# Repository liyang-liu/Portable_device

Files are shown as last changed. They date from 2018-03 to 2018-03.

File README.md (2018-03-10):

# Portable_device

This is the website containing details for the "Portable Lifting Device" project as a joint project with studendents enrolled for Mechanical and Mechatronic 3 at University of Technology, Sydney.

The project has been successfully attempted by the 2017-Spring team (Mobitronic) and 2017-Autumn team (UP Engineering). 
In particular, Mobitronic has envestigated on the subject thoroughly and explored both pneumatic concept and  mechanical concept. A prototype pneumatic demo was made with an [inflatable matress](https://drive.google.com/file/d/0B8edSPbUCKdPTHlibjlWQjhMN2M). For meachnical design, a [scissor jack stool drawing](https//github.com/liyang-liu/Portable_device/src/2017_Autumn_Mobitronic/scissor_jack_concept.mp4) is developed with detailed force/pressure calculation.
The UP Engineeirng team has manufactured a [portable airbag](https://youtu.be/5JIshlNcmgY).

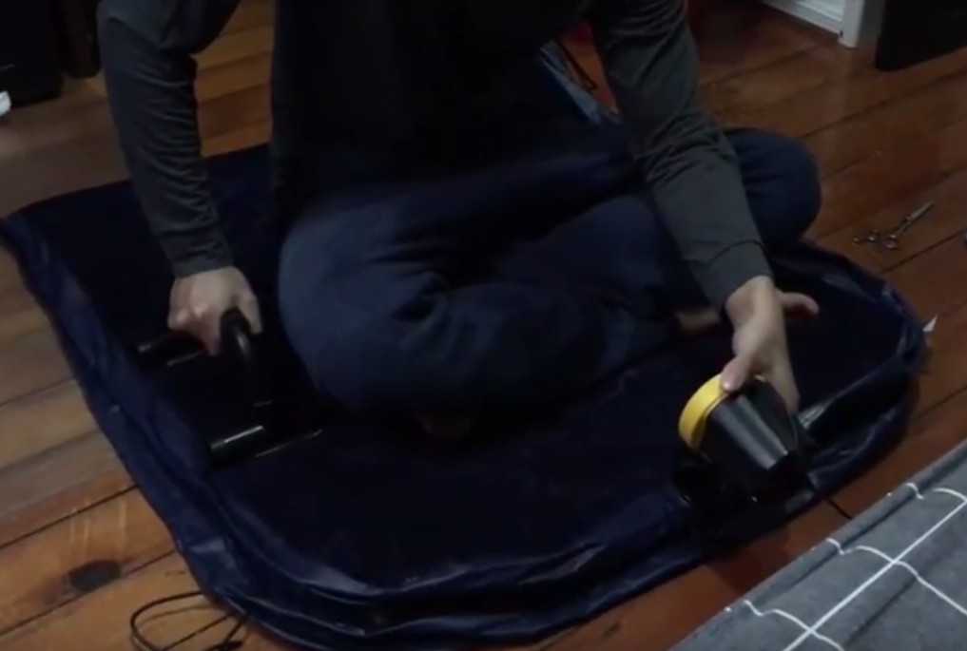
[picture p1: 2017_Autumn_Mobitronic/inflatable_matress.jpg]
inflatable_matress

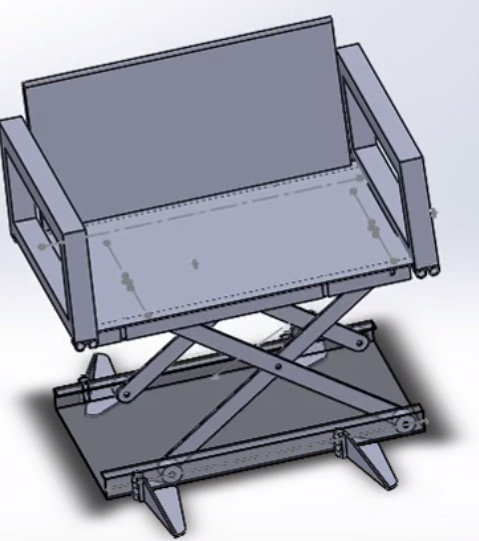
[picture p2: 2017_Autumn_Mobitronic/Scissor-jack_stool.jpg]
scissor-jack

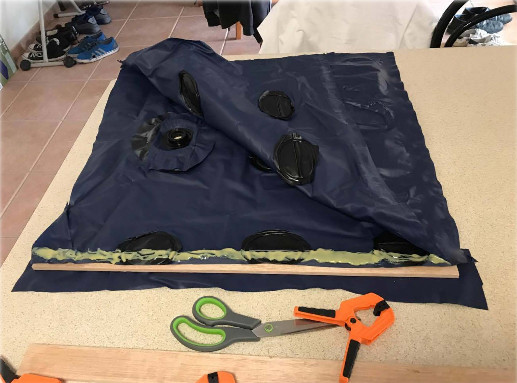
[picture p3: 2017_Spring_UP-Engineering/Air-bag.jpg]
portable_airbag


# 1. Prerequisites
Solidworks

# 2. Specification
Detailed specification is given in word document "Project_for_Lifting_airbag_spring-semester.docx"

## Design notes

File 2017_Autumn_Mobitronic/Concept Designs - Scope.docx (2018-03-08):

# Concept Designs – Scope

Team Mobitronic (13): Project: Portable Lifting Device

Renay Jewo (11443468) – Mechanical Engineer Client: Liyang Liu

Kunxian Huang (11671512) – Mechanical Engineer Project Start Date: 20/03/17

Bikrom Saha (11775677) – Mechanical Engineer Project Completion Date: 19/06/17

Viet Hung Doan (11808211) – Mechatronic Engineer

# Airbag Solution Concept Design

- Air-Bag Lifting mechanism will be connected to the client’s wheelchair from the back using connecting rods. The lifting device will contain a circular airbag that will be meshed between two platforms as shown below.
- The Air-Bag lifting capacity is more than sufficient to carry the patient. The Air-Bag will be inflated whilst the patient is seated using an Electric Pump that will be actuated by the patient using a toggle switch to pump and another to deflate.
- Transfer from surface to surface will be facilitated by the inclusion of hand-rails on either side of the top platform as depicted.
- Example air bag:

http://12.188.149.117/categories/lifting_air_bags/lowmedliftbags.aspx

Advantages | Disadvantages
Robust to hold weight of patient | Weight (Heavy) – Due to Electric Pump and Air Bag (Weight:Lifting Capacity Ratio)
Transported using wheelchair (Has wheels) | Not Hand-Portable – Will weigh more than 13kg
Electrically Operated (Electric Pump and Switches) – Easy to use and operate | Requires minor modification to wheelchair (Latch to connect lifting device)
Gradual raising of patient (not jolty)

# Alternative Hydraulic/Mechanical Concept Design (Hydraulic Jack)

- Hydraulic Jack used between two platforms to raise and lower the client to the specified heights of a wheelchair (500mm) and a kayak (350mm).
- Hydraulic Jack will be manually operated to raise and lower the platform by the patient. This doesn’t necessarily require much effort.
- The lifting device can in this case be smaller in dimensions, this will reduce the weight due to negating the electric pump and batteries from the design above.
- The topology of the design will be the similar to the air-bag lifting device in that it will be dragged behind the wheelchair and attached using a latch.

Advantages | Disadvantages
Lightweight Design | Hand-Operated (Manual Operation)
No external accessories such as a pump or heavy materials | Requires minor modification to wheelchair (Latch to connect lifting device)
Cheap and easy to operate, Height easily controlled
Transported using wheelchair

Airbag Proof of Concept – Testing

- We will be purchasing an inflatable mattress/airbag to simulate the effects and dynamics of raising and lowering the patient from deflation (once the patient is seated) to inflation.
- We will find a suitable pump to use within this experiment to provide enough pressure to lift the patient based on the specifications provided and to the required heights.
- This is just an experiment to determine the pressure required lift the patient.

Concept Designs – Specifications/Needs

The following specifications and functional requirements below are based on approximate values and are here to provide an indication and to accentuate the above advantages and disadvantages of each concept design.

| Airbag Concept Design | Hydraulic Concept Design
Weight (kg) | Gross Weight: ~15kg AirBag: 7kg Electric Pump: 3.9kg Batteries: 2kg Extras: 3kg | Total Weight: >5kg
Costs ($) | $2,500 | $300
Size (mm) | 800 x 600 x 250 | 600 x 600 x 200
Ease-of-use | Moderate | Easy

Questions to be clarified with stakeholder

1. Why is the lifting device needed?
2. What are the uses cases:
  1) Helps user to transfer to kayak
  2) 2nd scenario? To help user transfer to wheelchair in event of fall
3. Need to get a storyboard of user’s daily activity, to help understand motivation, use case and how the design can best suit user needs
4. How portable should the device be? Pump, power may take a lot of weight
  1) Will the device be carried independently by user for set up with other assistance?
5. Is a platform needed for the airbag to reside on top?

Portable Lifting DeviceTeam Mobitronic (13) 02/04/17

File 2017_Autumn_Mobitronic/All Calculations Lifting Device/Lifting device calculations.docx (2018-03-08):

# Lifting device calculations

The dimensions in this report base on the CAD model updated on 29 May 2017.

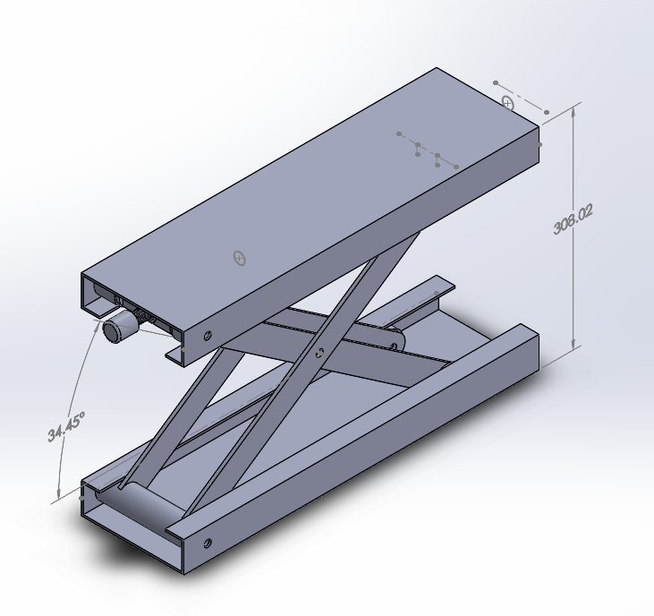
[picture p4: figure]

# Assumptions

Choosing lead screw SFU 3210-3 for initial calculations:

- Pitch diameter: 16mm
- Lead: 10mm
- Dynamic loading: 729kg
- Static loading: 1350kgf

Friction coefficient between steel screw and steel balls with machine oil: 0.15

User weight (W): 1000N (~101kg)

# Calculate Linear Force Acting on Lead Nut

Rx2

ti

ti

W

Rx2=w/(tan⁡(ti)) (see appendix for step by step)

The requirement height varies from 150mm to 500mm corresponding to ti from 13.28 to 78.66 degree.

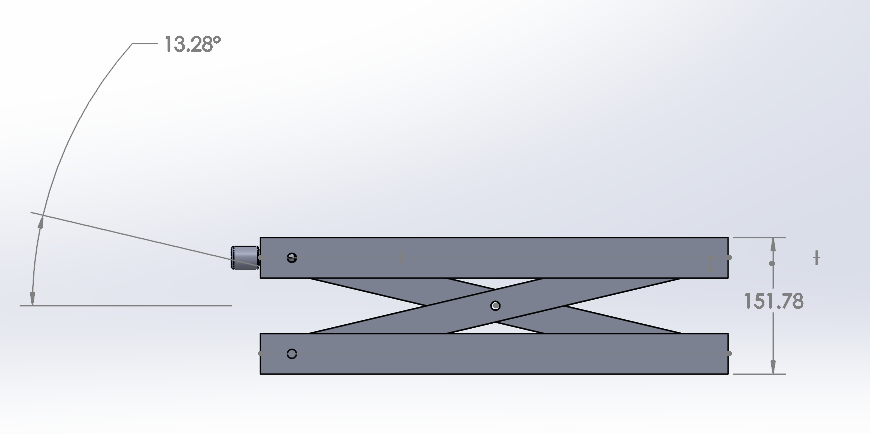
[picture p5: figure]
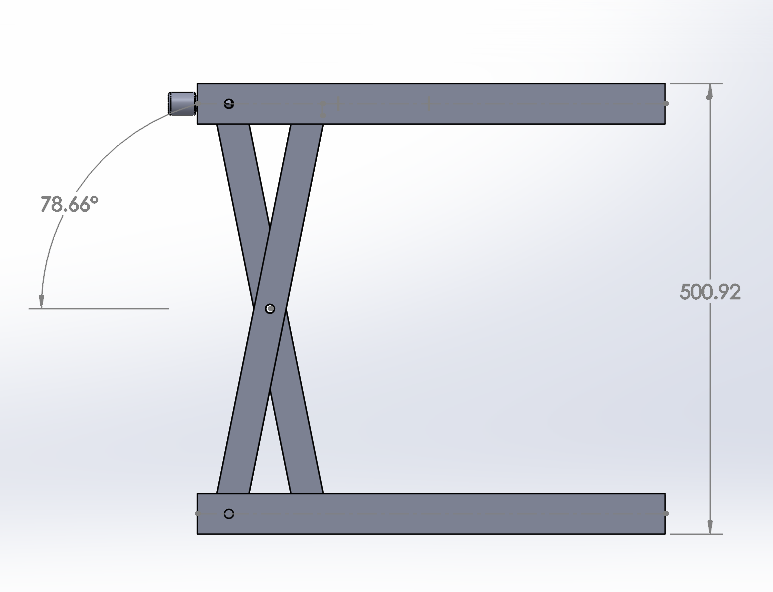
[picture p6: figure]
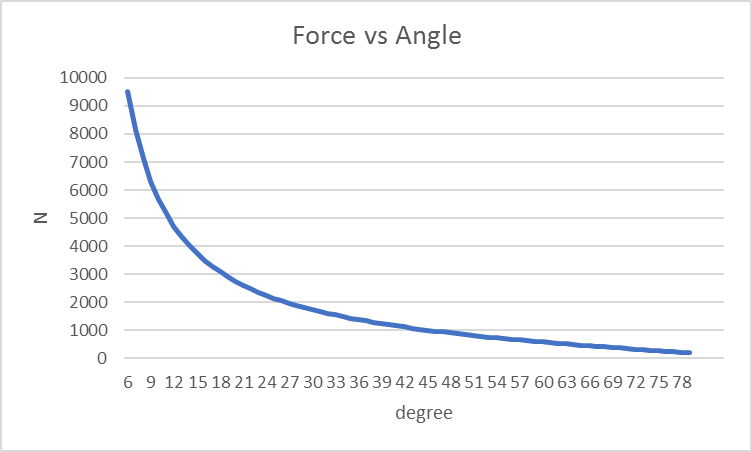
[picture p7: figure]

Critical force occurs when the jack is at its lowest position, ti= 13.28 N= 4236 N.

# Calculate Torque Required on Lead Screw

Adopt equations for trapezoidal thread from Wiki (https://en.wikipedia.org/wiki/Leadscrew)

Where:

- T = torque
- F = load on the screw
- dm = pitch diameter
- μ = coefficient of friction (common values are found in the adjacent table)
- l = lead
- λ = lead angle

Maximum Torques:

Traise = 8.58 Nm

Tlower = -1.74 Nm (sign indicates opposite direction)

Assuming the handle arm (r) is 0.2m, the maximum required input is: F=T/r=42.9 N ≈4.4 kg

# Calculate Number of Turns

From lowest to highest position, the lead nut must travel: 360 mm.

No.of Turns=s/(lead)=360/10=36

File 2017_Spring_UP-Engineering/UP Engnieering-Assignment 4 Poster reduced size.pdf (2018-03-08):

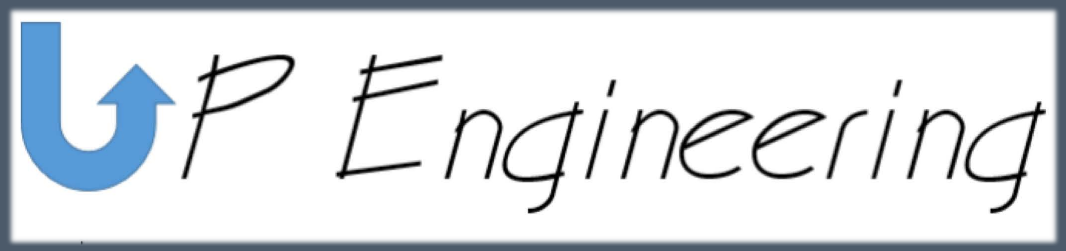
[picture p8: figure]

### PROJECT: Portable Lifting Air-Bag CLIENT: LiYang Liu TEAM: Angelo Rafaraci (98137577), Steve Astorga (11971658) & Jude Outschoorn (12031415)

## THE PROJECT STATEMENT

Transferring from low to high surfaces can be extremely difficult for paraplegics. This is because of the physical strength and agility required to lift oneself and transfer to the desired platform. The requirement to move between a wheelchair and beds, shower chairs, and in this case a kayak translates to a frequent motion necessary for any lifestyle. Hence, the health risks associated with unsafe and strenuous transfer methods form the basis for our design focus. UP Engineering set out to create a design solution that would allow a paraplegic to safely and easily transfer between platforms while further contributing to an unassisted lifestyle.

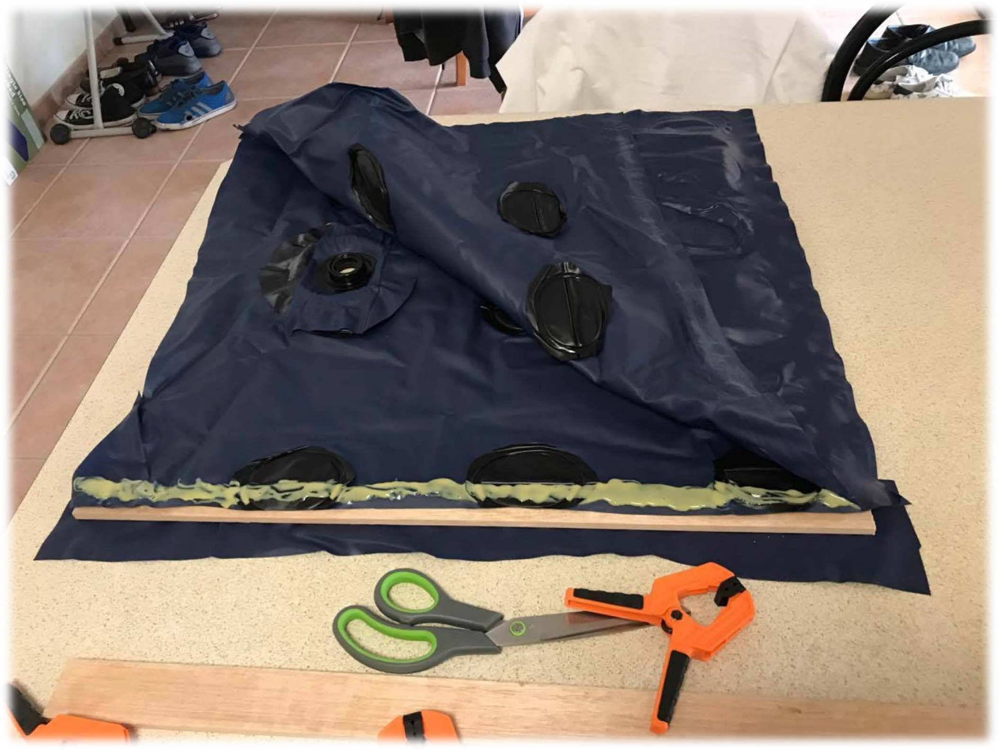
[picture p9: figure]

## RESEARCH

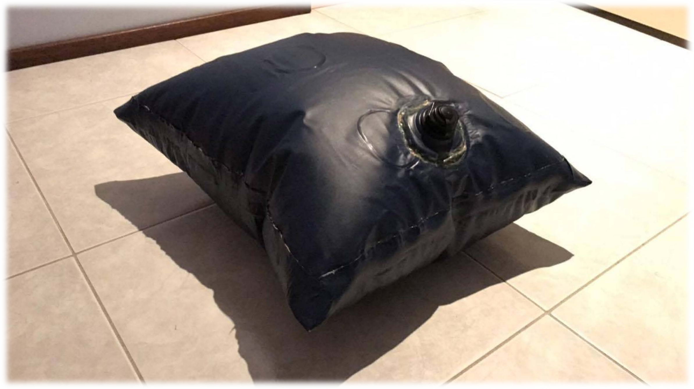
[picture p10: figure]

- Initial consultation with Occupational Therapist Monika Caraballo emphasized safety concerns with unassisted paraplegic transfer methods, often leading to unnecessary bruising and strain on the individual’s body.
- Market analysis presented a range of hoist-mechanisms, with pneumatic lifting aids only catering to emergency situations.
- The need for stability and device uses per charge would determine the independent and portable use of the device in the real world.

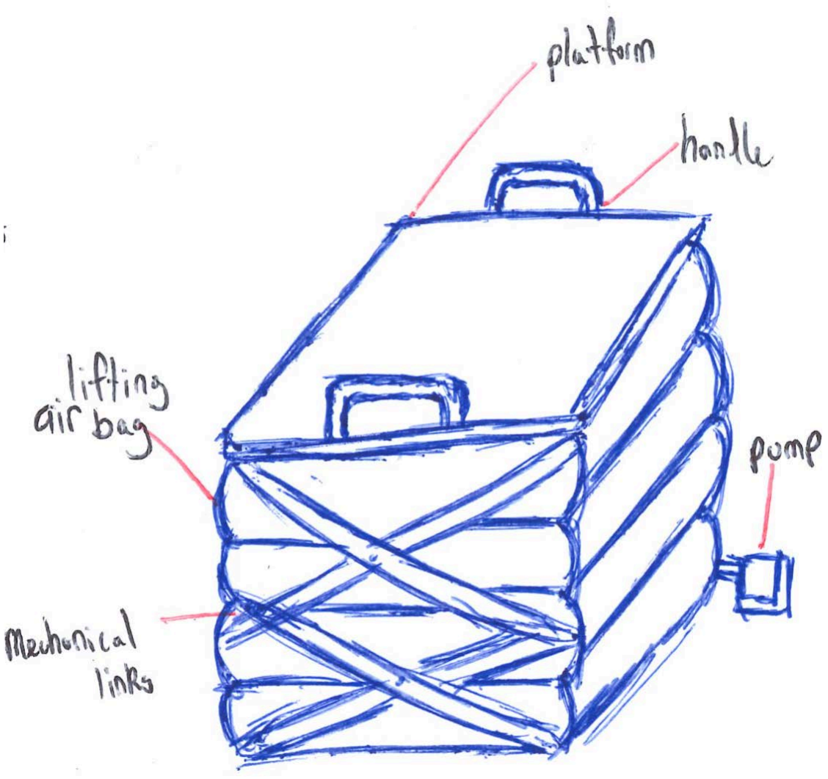
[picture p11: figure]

## DESIGN OBJECTIVES

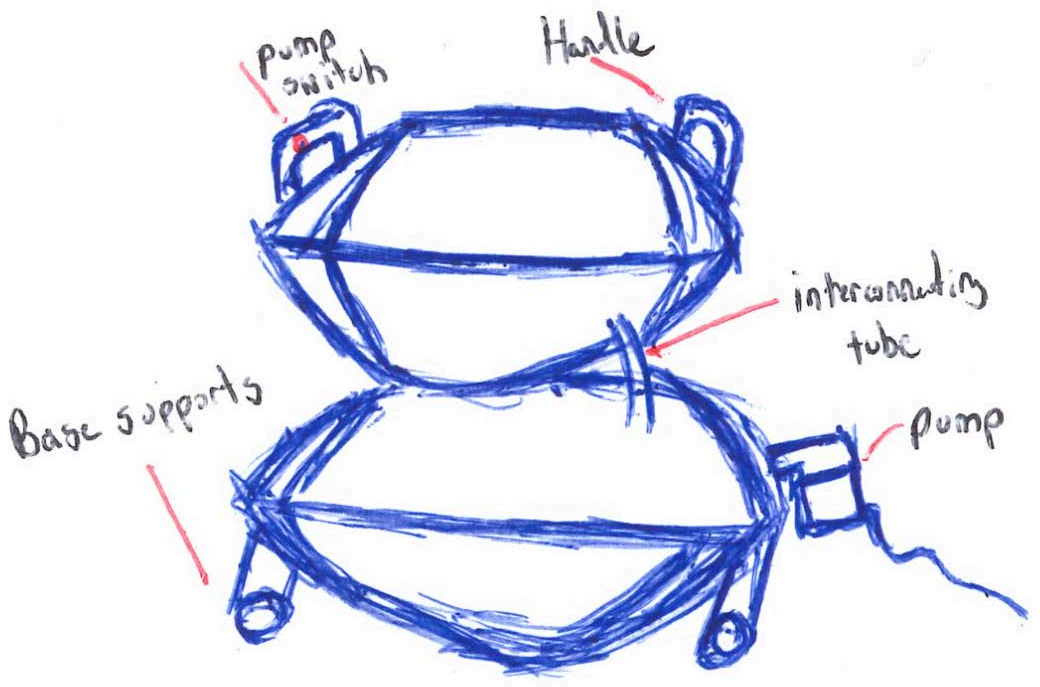
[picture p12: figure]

- User is able to safely transfer independently
- Lifting capacity of up to 100kg
- Device weight between 3-5kg
- 2-3minute total transfer time
- Easily accessible from the wheelchair
- Portable and compact (battery powered)
- Easy to maintain

## IDEATION AND DEVELOPMENT

- Design objectives essentially aimed to prevent the following strenuous motion. UP engineering had a basic concept in mind after talks with the client. :

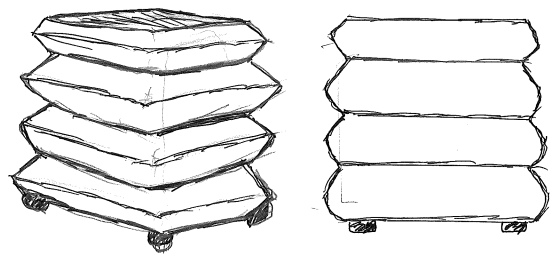
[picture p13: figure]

- Initial sketching allowed us to visualise what needed to be made. Critically, the individual control of each layer was necessary for stable lifting :

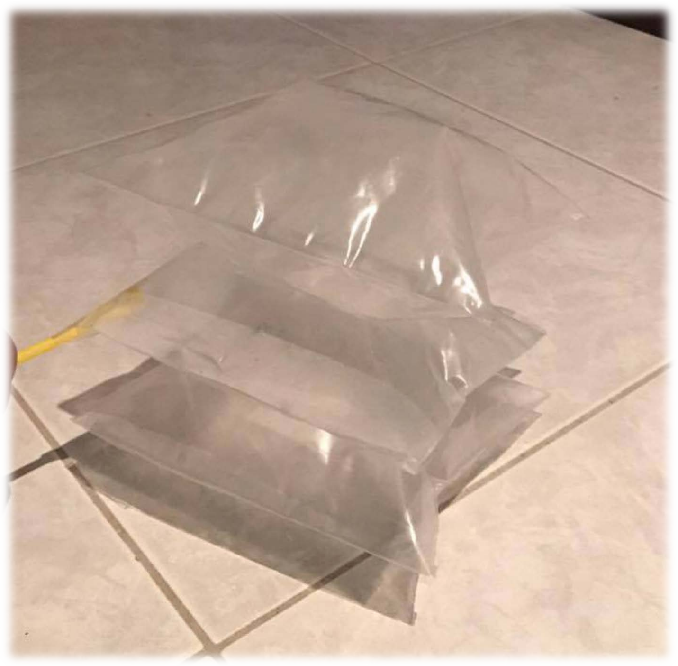
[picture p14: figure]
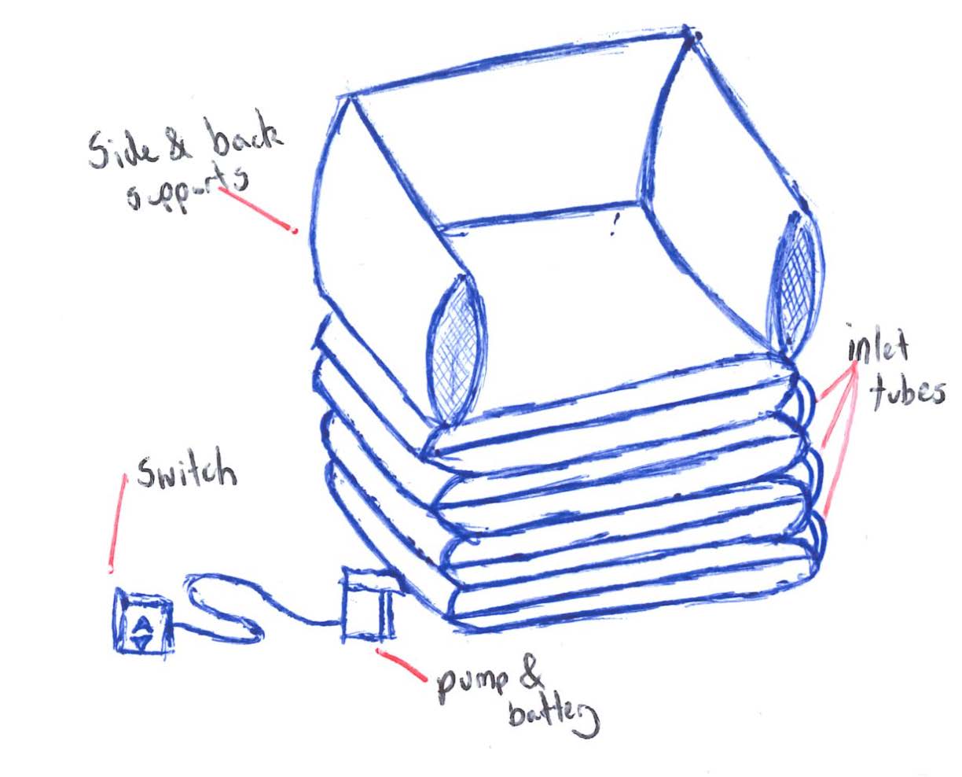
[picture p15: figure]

- Stabilisation methods included handles and parallel stiffeners:

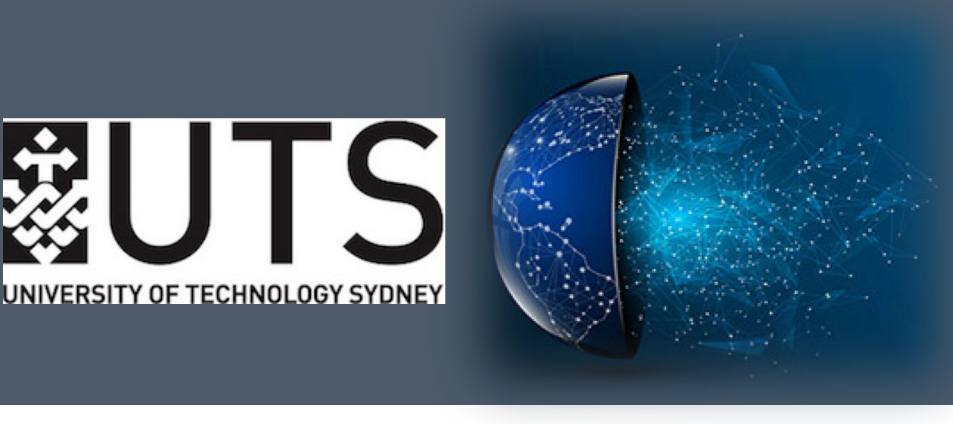
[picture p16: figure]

## PROTYPING AND TESTING

## RECOMMENDATIONS

- Further research is needed in obtaining a battery powered air pump capable of achieving multiple uses with a single charge.
- Stability mechanism must be finalised in order to achieve safe use while maintaining compact size.

With sufficient research and design development, we were able to produce a reliable proof of concept:

Testing critical requirements included:
- Joining methods – flexibility, durability and sealing were all major components being tested.
- Air pump – testing the ability of various air pumps to inflate the loaded device and achieve ‘lift’.

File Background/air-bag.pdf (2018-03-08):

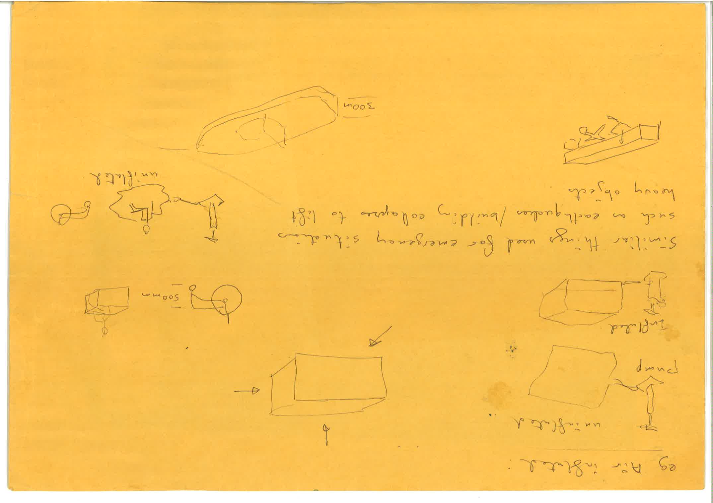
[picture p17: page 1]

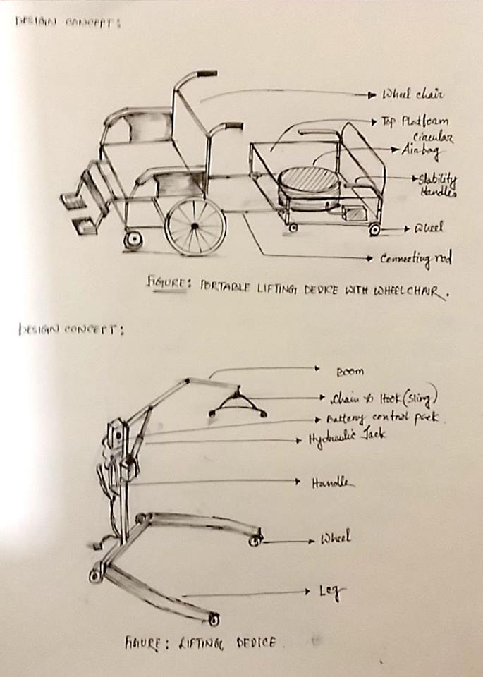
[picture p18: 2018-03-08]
2017_Autumn_Mobitronic/Mobile-tronic_initial_mechanical-drawing.jpg

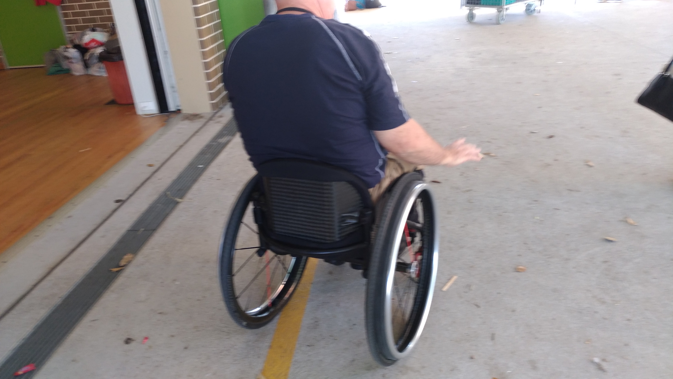
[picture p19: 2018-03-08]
Background/wheel-chair/P_20170423_114121_vHDR_Auto.jpg

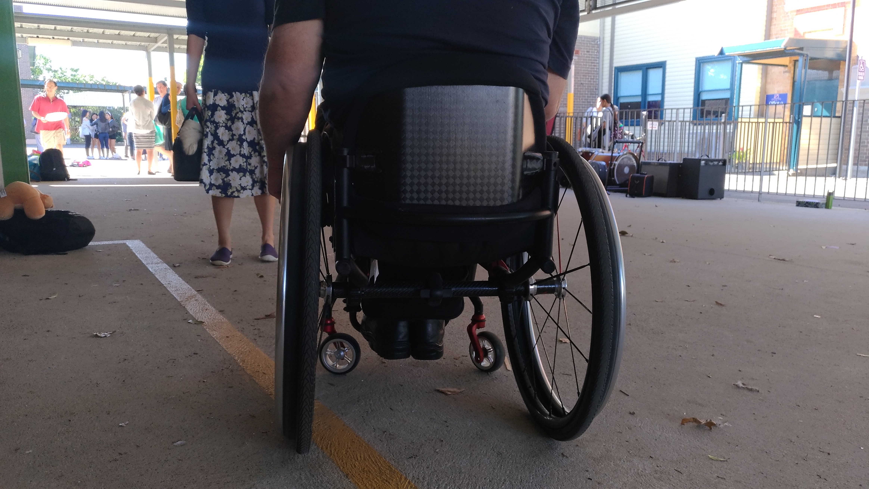
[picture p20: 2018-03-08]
Background/wheel-chair/P_20170423_114058_vHDR_Auto.jpg

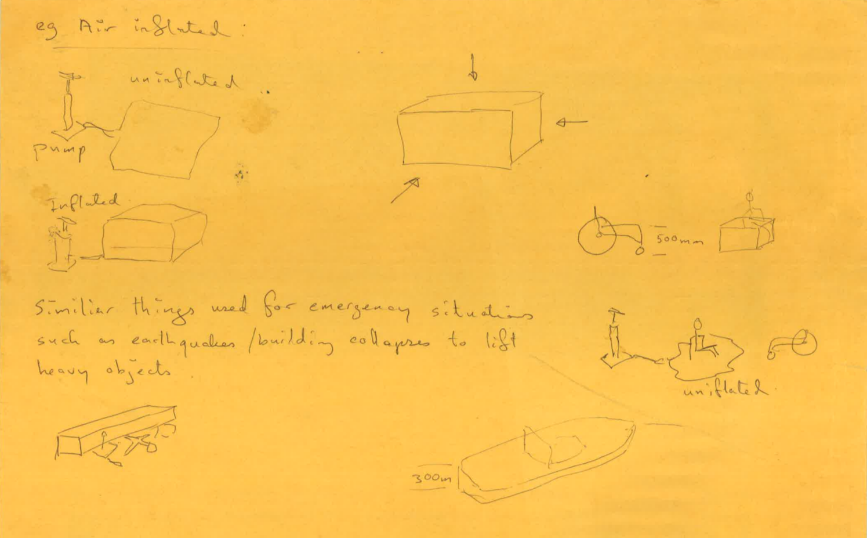
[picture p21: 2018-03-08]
Background/air-bag.png

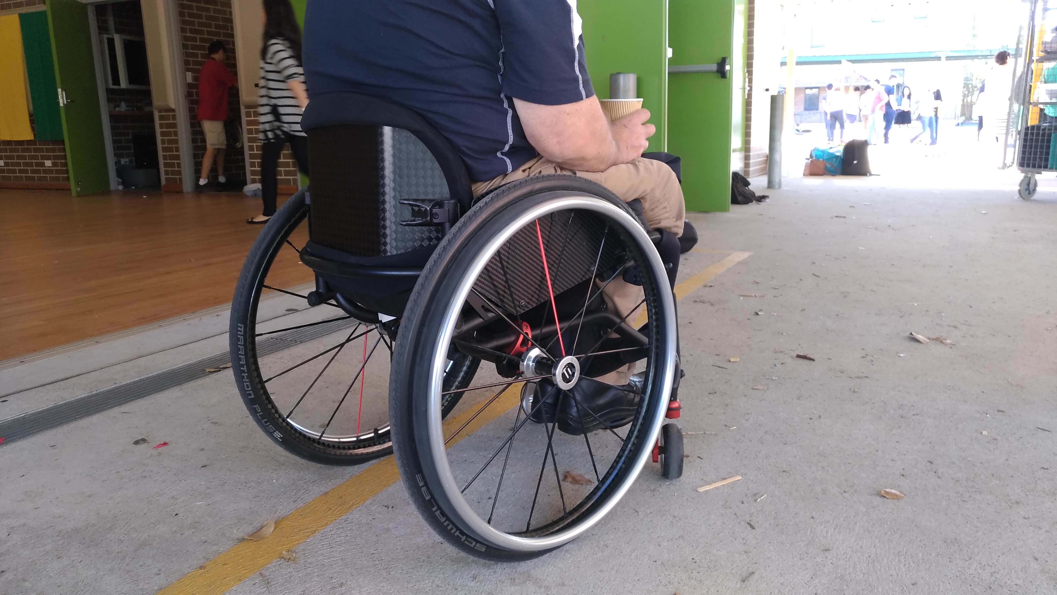
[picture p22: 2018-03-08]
Background/wheel-chair/P_20170423_114108_vHDR_Auto.jpg

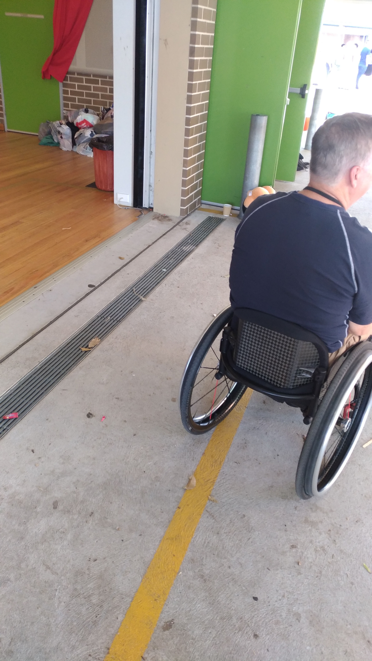
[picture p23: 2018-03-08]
Background/wheel-chair/P_20170423_114148_vHDR_Auto.jpg

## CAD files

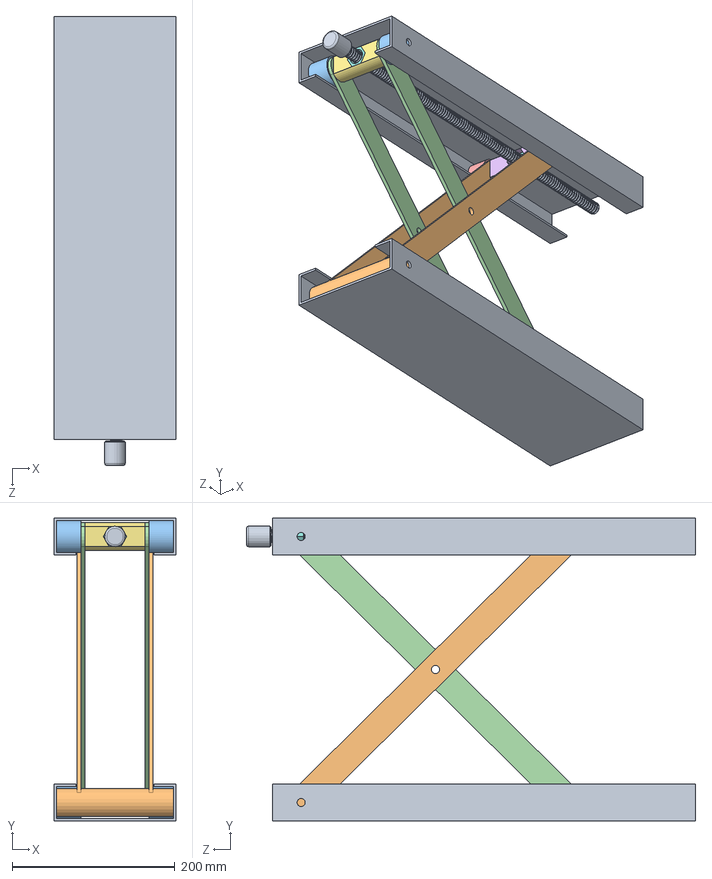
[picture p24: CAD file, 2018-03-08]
2017_Autumn_Mobitronic/secissor jack/Assem4.SLDASM
150.0 x 372.2 x 552.2 mm
base bottom x 2
bottom s
bottom wheel x 4
side pan x 2
top wheel x 2
back screw pan
front screw pan
nut with thread x 2
thread rod

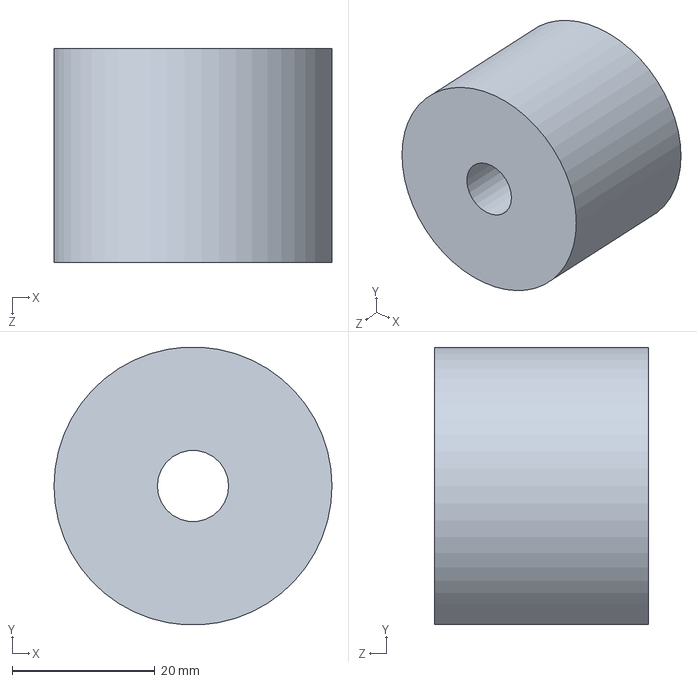
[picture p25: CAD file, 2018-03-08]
2017_Autumn_Mobitronic/secissor jack/bottom wheel.SLDPRT
39.0 x 38.9 x 30.0 mm

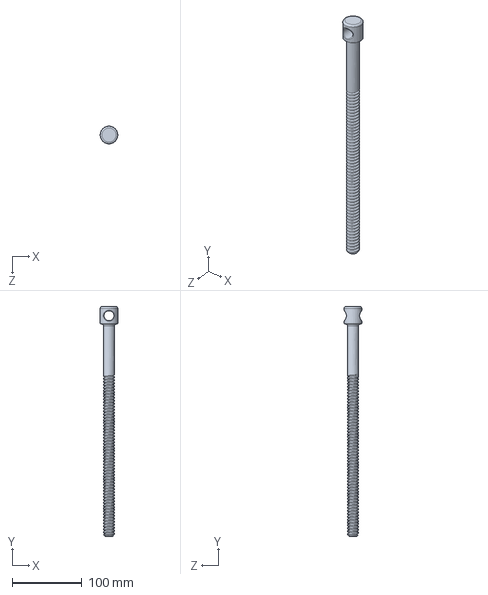
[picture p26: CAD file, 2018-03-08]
2017_Autumn_Mobitronic/secissor jack/New Folder/Tornillo_acme_PASO6.SLDPRT
25.4 x 330.2 x 25.4 mm

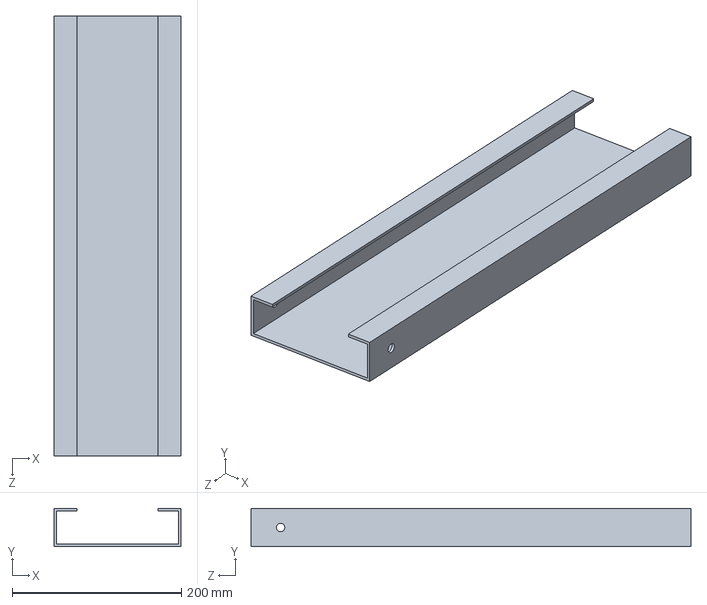
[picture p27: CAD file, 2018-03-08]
2017_Autumn_Mobitronic/secissor jack/base bottom.SLDPRT
150.0 x 45.0 x 520.0 mm

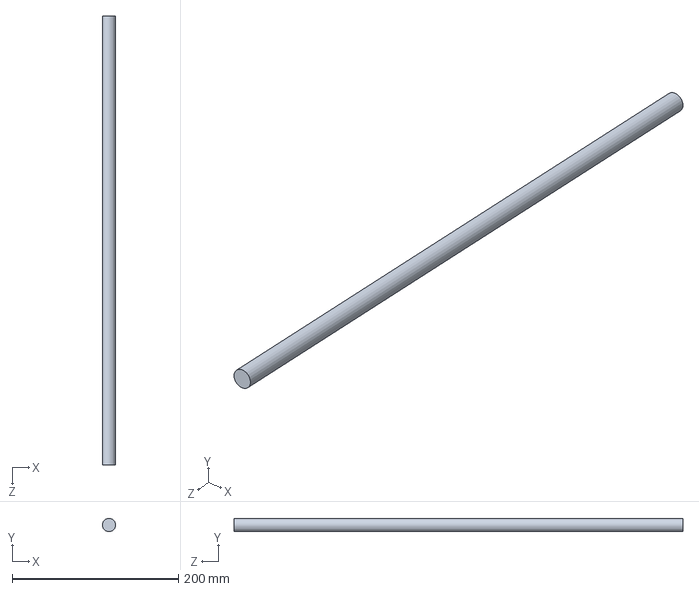
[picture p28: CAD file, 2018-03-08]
2017_Autumn_Mobitronic/secissor jack/thread.SLDPRT
16.0 x 16.0 x 540.0 mm

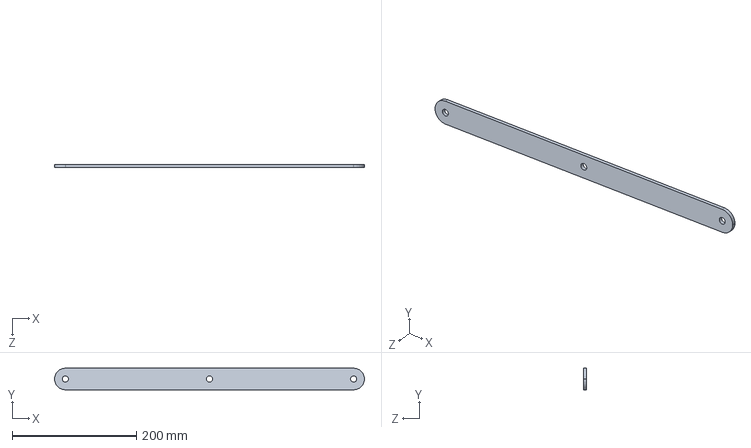
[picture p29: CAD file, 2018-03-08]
2017_Autumn_Mobitronic/secissor jack/side pan.SLDPRT
500.0 x 35.0 x 5.00 mm

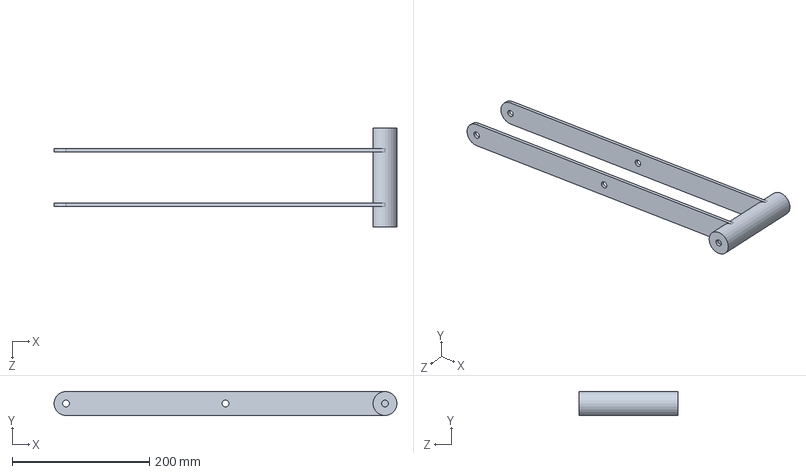
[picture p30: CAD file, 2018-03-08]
2017_Autumn_Mobitronic/secissor jack/top s.SLDPRT
500.0 x 35.0 x 144.0 mm

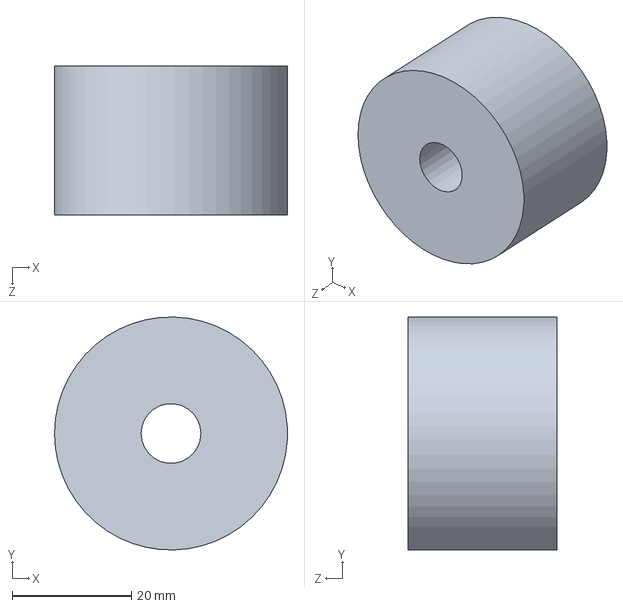
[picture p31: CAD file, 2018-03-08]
2017_Autumn_Mobitronic/secissor jack/top wheel.SLDPRT
39.0 x 39.0 x 25.0 mm

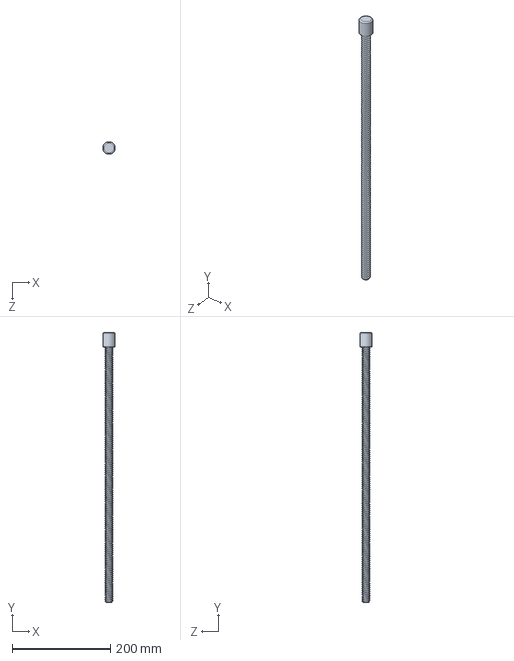
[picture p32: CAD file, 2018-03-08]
2017_Autumn_Mobitronic/secissor jack/thread rod.SLDPRT
25.4 x 550.0 x 25.4 mm

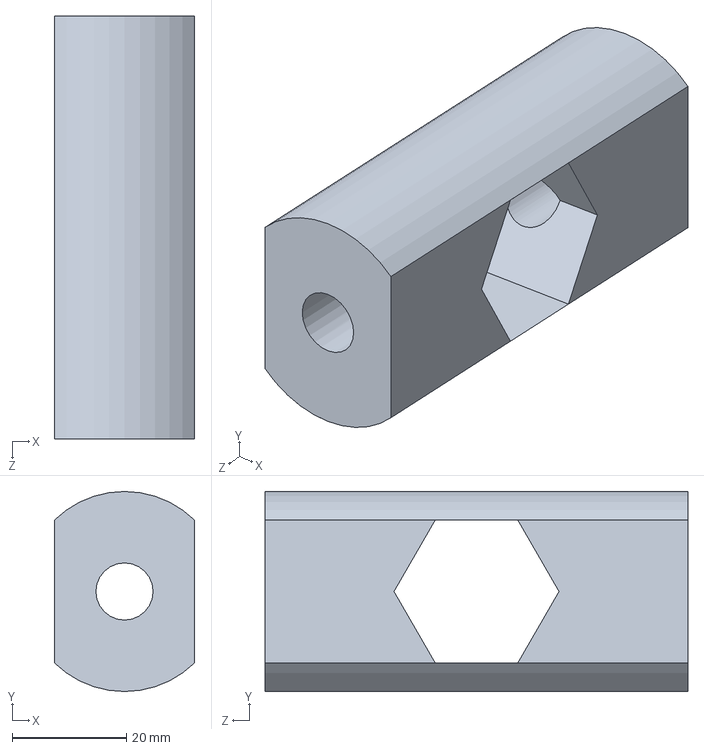
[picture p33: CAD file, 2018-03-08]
2017_Autumn_Mobitronic/secissor jack/front screw pan.SLDPRT
24.5 x 35.0 x 74.0 mm

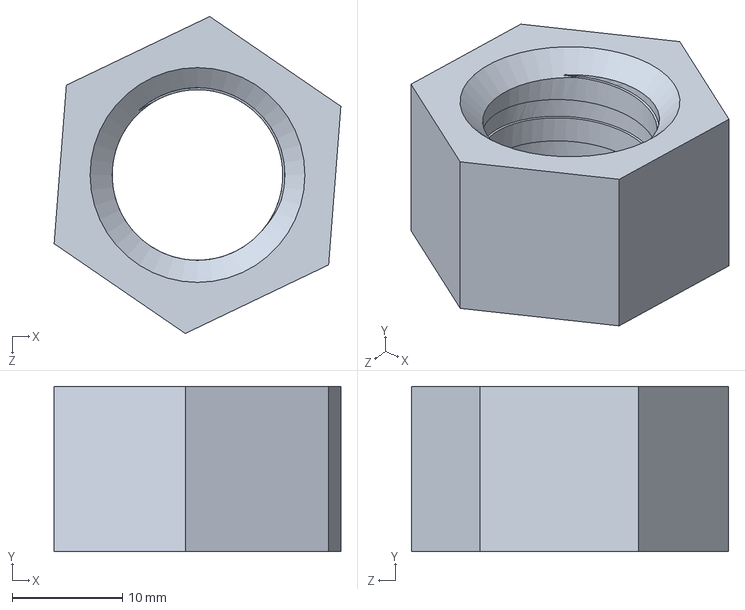
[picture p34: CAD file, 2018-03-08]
2017_Autumn_Mobitronic/secissor jack/New Folder/nut with thread.SLDPRT
26.0 x 15.0 x 28.8 mm

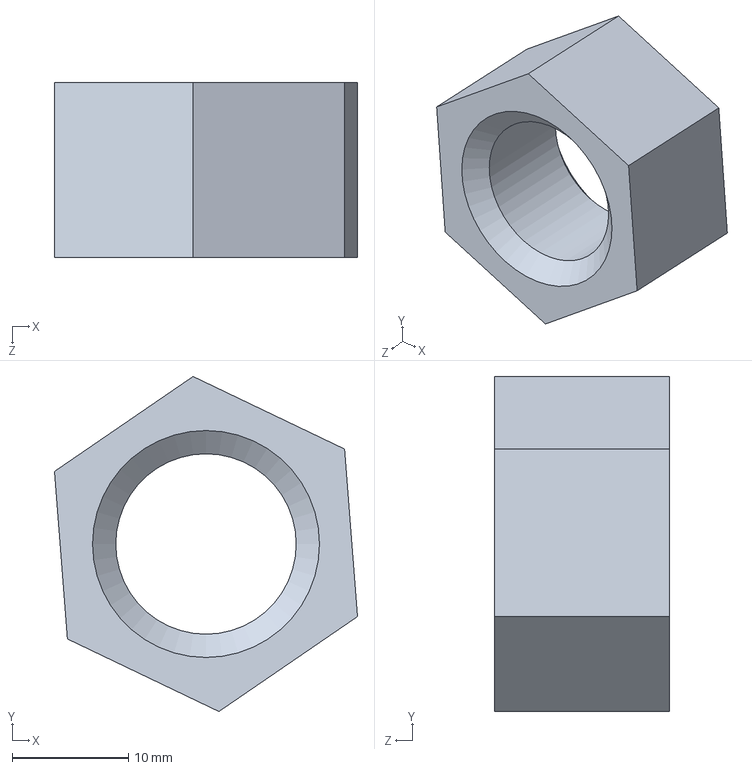
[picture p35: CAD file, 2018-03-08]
2017_Autumn_Mobitronic/secissor jack/New Folder/nut.SLDPRT
26.0 x 28.8 x 15.0 mm

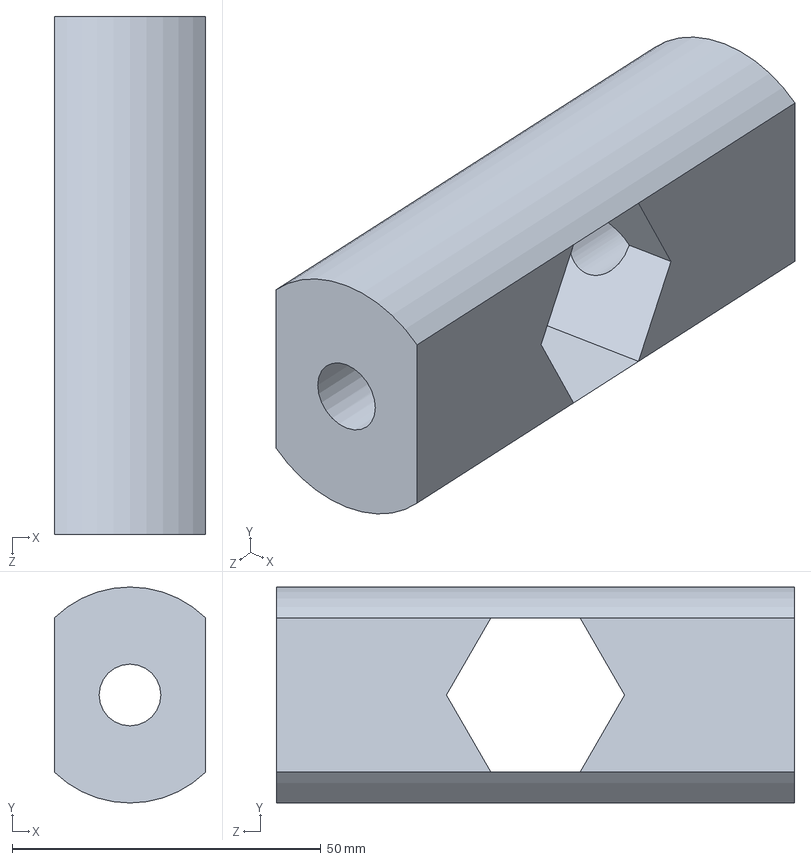
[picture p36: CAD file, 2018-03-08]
2017_Autumn_Mobitronic/secissor jack/back screw pan.SLDPRT
24.5 x 35.0 x 84.0 mm

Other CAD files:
2017_Autumn_Mobitronic/secissor jack/bottom s.SLDPRT
